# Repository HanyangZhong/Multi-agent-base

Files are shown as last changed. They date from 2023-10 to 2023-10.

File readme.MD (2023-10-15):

# 1.Hardware connection of the burgerbot drive board
d442afaf809981fc043d6bcae772b21
821f4247668aef92b34aded4d3898d7

## Connecting the drive board TB220A1

Take the driver board from the front, with the switch facing the left hand position        
Take this as a positive aspect        


The motor on the left is the right motor 'PWMB' timing in the encoder1 code corresponding to 'PWMB', with a default direction of forward rotation
The motor on the right is the left motor 'PWMA' timing in the encoder1 code corresponding to 'PWMA', with the default direction turning backwards

## Wire Connection：
The input terminal of the drive board is connected to a power supply of less than 15V, preferably 12V        
The corresponding motor is 'MG513P30_ 12V'        
        
Left white slot connected to the physical position of the car, left motor        
Right white slot connected to the physical position of the car Right motor        
        
EncoderIO：        
```
GND -- arduino mega GND
E2A  -- arduino mega 19
E2B  -- arduino mega 18
E1A  -- arduino mega 21
E1B  -- arduino mega 20
5V  None
```

c3236ec6e28d0965030df91bf430cfb
7beadca7b2e9b9cac09d8948b6bce38



DriverBoardIO：        
```
PWMB -- arduino mega 10
BIN2  -- arduino mega 9
BIN1  -- arduino mega 8
STBY  -- arduino mega 7
AIN1 -- arduino mega 5
AIN2 -- arduino mega 4
PWMA -- arduino mega 3
```

# 2.Arduino wire connection Test
## 1. Motor rotation test
Test whether the two motors can rotate normally using the 'TB6612motor' Arduino project          

## 2. Encoder testing
Use 'encoder1' as the Arduino project to test the readings of two encoders separately        

```
// motor1
//int motor_A = 21;//Interrupt port is 2
//int motor_B = 20;//Interrupt port is 3
//motor2
int motor_A = 18;//Interrupt port is 5
int motor_B = 19;//Interrupt port is 4

//Annotate the other when using pairs
...

void setup() {
  Serial.begin(57600);//
  pinMode(motor_A,INPUT);
  pinMode(motor_B,INPUT);
//
//  attachInterrupt(2,count_A,CHANGE);//Trigger interrupt function when level changes
//  //Quadruple frequency statistics require adding interrupts for phase B as well
//  attachInterrupt(3,count_B,CHANGE);

  attachInterrupt(5,count_A,CHANGE);//Trigger interrupt function when level changes
  //Quadruple frequency statistics require adding interrupts for phase B as well
  attachInterrupt(4,count_B,CHANGE);
}

```

# 3.Arduino Bridge Test
By configuring the wiring and IO port of 'TB220A1', you can directly burn and write the arduino bridge file to 'Mega2560', and then start testing        
## 1.Test encoder rotation
'e' is the number of test encoders        
'r' is the reset encoder count        
After testing the left and right wheels in the correct direction and direction, proceed to the next step of testing        
        



## 2.Test motor drive
'm' is motor speed control        
'm 100 0' is the forward movement of the left motor at a speed of 100 seconds        
Then set 'm 0 0'        



## 3.PID debugging
After testing the motor rotation and encoder function, start testing the PID        
In diff_ Under controller. h, change the test PID parameters        
Test doPID left and right wheels separately, remember to uncomment and restore after testing is completed        

```

SetPointInfo leftPID, rightPID;

/* PID Parameters */
int Kp = 17;
int Kd = 13;
int Ki = 0;
int Ko = 50;

...

void doPID(SetPointInfo * p) {
  long Perror;
  long output;
  int input;

  //Perror = p->TargetTicksPerFrame - (p->Encoder - p->PrevEnc);
  //Real time speed=Current encoder value - Last encoder end value (1/30 seconds)
  input = p->Encoder - p->PrevEnc;
  // Error=target value - current speed value
  Perror = p->TargetTicksPerFrame - input;
    //Print and use a serial plotter to test and adjust the pid
//  Serial.println(input);/

....

//Adjust the pid of the left and right wheels separately
  //doPID(&rightPID);
  doPID(&leftPID);

```

## 4.Ros-arduino-bridge yaml File Configuration
The main startup files are in 'ROS_Arduino_Bridge/Ros_Arduino_Python/launch'.        
Among them, 'my_ arduino_params' is the default file name        
Copy and rename under 'config', enter the following parameters        
```
# For a direct USB cable connection, the port name is typically
# /dev/ttyACM# where is # is a number such as 0, 1, 2, etc
# For a wireless connection like XBee, the port is typically
# /dev/ttyUSB# where # is a number such as 0, 1, 2, etc.

port: /dev/ttyACM0 #Set as appropriate, usually set to/dev/ttyACM0 or/dev/ttyUSB0
baud: 57600 #
timeout: 0.1 #

rate: 50
sensorstate_rate: 10

use_base_controller: True  #Enable Base Controller
base_controller_rate: 10   

# For a robot that uses base_footprint, change base_frame to base_footprint
base_frame: base_footprint #base_frame set up

# === Robot drivetrain parameters
wheel_diameter: 0.085 #Wheel diameter
wheel_track: 0.212    #0.244 -0.032 #Wheel spacing
encoder_resolution: 1560 #Encoder accuracy (number of pulses per cycle * frequency doubling * deceleration ratio)
#gear_reduction: 1 #reduction ratio
#motors_reversed: False #Reverse steering

# === PID parameters PID Parameters that need to be adjusted by oneself
Kp: 17
Kd: 13
Ki: 0
Ko: 50
accel_limit: 1.0

# === Sensor definitions.  Examples only - edit for your robot.
#     Sensor type can be one of the follow (case sensitive!):
#      * Ping
#      * GP2D12
#      * Analog
#      * Digital
#      * PololuMotorCurrent
#      * PhidgetsVoltage
#      * PhidgetsCurrent (20 Amp, DC)

sensors: {
  #motor_current_left:   {pin: 0, type: PololuMotorCurrent, rate: 5},
  #motor_current_right:  {pin: 1, type: PololuMotorCurrent, rate: 5},
  #ir_front_center:      {pin: 2, type: GP2D12, rate: 10},
  #sonar_front_center:   {pin: 5, type: Ping, rate: 10},
  arduino_led:          {pin: 13, type: Digital, rate: 5, direction: output}
}

```

Before running the bridge's launch file, it is necessary to 'ros_arduino_python/nodes/arduino_node.py' Setting executable permissions for files under 'node.py'        
```
sudo chmod +x arduino_node.py
```

# 4.Distributed communication configuration
## 0.Wifi Connections setting up        
1.Hardware preparation: Use a display screen or HDMI acquisition card to connect to Raspberry Pi and start it;        
2.Connect the Raspberry Pi to a wireless network;        
3.Configure static IP for Raspberry Pi, as shown in the figure        





## 1.System File Configuration
### Necessary dependency installation
The SSH implementation architecture is divided into two parts: client and server. The client is the sender of data, and the server is the receiver of data.         
In the current scenario, we need to send data from the PC to Raspberry Pi. Therefore, the PC belongs to the client, while Raspberry Pi belongs to the server. The specific implementation process is as follows:        
1. Install SSH client and server separately
2. Start SSH service on the server
3. Remote login of the client to the server
4. Implement data transmission
#### 1.Install SSH client and server        
By default, the Ubuntu system already has an SSH client installed, so you only need to install the server on Raspberry Pi (if Raspberry Pi is installing a service version of Ubuntu, the SSH service will be installed by default and has been set to boot automatically):        
```
sudo apt-get install openssh-server
```
If the client needs to install itself, call the following command:        
```
sudo apt-get install openssh-client
```
#### 2.Start SSH service on the server
Raspberry Pi Start SSH Service:        
```
sudo /etc/init.d/ssh start
```
Check if the service is running normally after startup:        
```
ps -e | grep ssh
```
If the startup is successful, it will include two programs: 'sshd' and 'ssh'.        
In the future, it is necessary to frequently use SSH to log in to Raspberry Pi. To simplify implementation, you can set the SSH service of Raspberry Pi to boot automatically. The command is as follows:        
```
sudo systemctl enable ssh
```
#### 3.Remote login of the client to the server
To log in to Raspberry Pi, you can call the following command:        
```
ssh Account@IP_address
```
Then, according to the prompt, enter the login password to successfully log in.        
If you exit the login, you can call the 'exit' command:        
```
exit
```
#### 4.Implement data transmission
Upload file:        
```
scp Local_file_path account@ip:Raspberry_path
```
Upload folder:        
```
scp -r Local_folder_path account@ip:Raspberry_path
```
Download files:                
```
scp account@ip:Raspberry_path Local_file_path    
```
Download folders:        
```
scp -r account@ip:Raspberry_path Local_folder_path
```
#### 3.Install Ros—Arduino-Bridge
'ROS_Arduino_Bridge' relies on the 'Python serial' feature pack. Please install this feature pack on the Raspberry Pi client first. The installation command is:            
```
sudo apt-get install python-serial
```
or            
```
sudo pip install --upgrade pyserial
```
or            
```
sudo easy_install -U pyserial
```

### configuration file    
Connect Raspberry Pi or Jetson Nano to the same WiFi network as the computer            
As 'PC: 192.168.0.101'          
As Raspberry Pi 'Pi: 192.168.0.110'            
Both the computer end and embedded controller end are set with static IPs to ensure they are in the same network segment        
Input        
```
sudo gedit /etc/hosts
```
Both the slave and host must be set        
Configure the other party's IP address        
```
127.0.0.1	localhost
127.0.1.1	zhy
192.168.0.110	raspberrypi

# The following lines are desirable for IPv6 capable hosts
::1     ip6-localhost ip6-loopback
fe00::0 ip6-localnet
ff00::0 ip6-mcastprefix
ff02::1 ip6-allnodes
ff02::2 ip6-allrouters
```

Then configure the ROS host and slave corresponding to the '. bashrc' file        
Enter 'sudo gedit. bashrc'        
Set the PC as a slave and take the main address of the host Raspberry        
```
export ROS_MASTER_URI=http://192.168.0.110:11311
export ROS_HOSTNAME=192.168.0.101
```
Set Raspberry Pi as the host, and take the address of the host Raspberry Pi as the main address        
```
export ROS_MASTER_URI=http://192.168.0.110:11311
export ROS_HOSTNAME=192.168.0.110
```

## 2.sshConnection control
Control commands such as:            
```
ssh -X wheeltec@192.168.0.110
```
Enter password and start controlling        

The host side run 'roscore', while the slave side does not need to run 'roscore' to send messages        
Note that all command lines require 'source. bashrc', otherwise the environment variables will not be refreshed        
Host side running test:        
```
roscore
rosrun turtlesim turtlesim_node 
```
Slave running test:        
```
rosrun turtlesim turtlesim_node 
```
After all tests are passed and messages can be received, you can start testing the arduino bridge control        

## 3.Remote control car test
### 1.Code transmission and compilation
Please first create a workspace on the Raspberry Pi end, enter the 'src' directory of the local workspace on the PC end, and call the program upload command:        
```
scp -r ros_arduino_bridge/ Raspberry_account@Raspberry_ip:~/workspace/src
```
Enter the workspace and compile on the Raspberry Pi end:        
```
catkin_make
```
### 2.test
Now start the Raspberry Pi program, and then start the PC program.        
#### Raspberry Pi
Start ros_arduino_bridge node:        
```
roslaunch ros_arduino_python arduino.launch
```
#### PC
Start keyboard control node：        
```
rosrun teleop_twist_keyboard teleop_twist_keyboard.py
```
If there are no abnormalities, you can now control the car's movement on the PC through the keyboard, and the PC can also use rviz to view the car's odometer information.

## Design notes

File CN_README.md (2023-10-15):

# 1.小车驱动板硬件连接
d442afaf809981fc043d6bcae772b21
821f4247668aef92b34aded4d3898d7

## 连接驱动板 TB220A1

正面拿驱动板，开关对着左手位置    
以此为正面    


左边的电机是 PWMB 对应encoder1代码里面的right电机    PWMB正时，默认方向向前转    
右边的电机是 PWMA 对应encoder1代码里面的left电机      PWMA正时，默认方向向后转    

## 接线：
驱动板输入端接15v以内电源，最好12v    
对应电机是MG513P30_12V    

左边白色插槽连小车物理位置左电机    
右边白色插槽连小车物理位置右电机    
    
编码器IO：
```
GND -- arduino mega GND
E2A  -- arduino mega 19
E2B  -- arduino mega 18
E1A  -- arduino mega 21
E1B  -- arduino mega 20
5V  不接
```

c3236ec6e28d0965030df91bf430cfb
7beadca7b2e9b9cac09d8948b6bce38



驱动IO：        
```
PWMB -- arduino mega 10
BIN2  -- arduino mega 9
BIN1  -- arduino mega 8
STBY  -- arduino mega 7
AIN1 -- arduino mega 5
AIN2 -- arduino mega 4
PWMA -- arduino mega 3
```

# 2.arduino测试
## 1. 电机转动测试
用 TB6612motor这个arduino工程分别测试两个电机是否能正常转动        

## 2. 编码器测试
用 encoder1这个arduino工程分别测试两个编码器的读数        

```
// 电机1
//int motor_A = 21;//中端口是2
//int motor_B = 20;//中断口是3
//电机2
int motor_A = 18;//中端口是5
int motor_B = 19;//中断口是4

//使用其中一个的时候注释另一个
...

void setup() {
  Serial.begin(57600);//设置波特率  
  pinMode(motor_A,INPUT);
  pinMode(motor_B,INPUT);
//使用其中一个的时候注释另一个
//  attachInterrupt(2,count_A,CHANGE);//当电平发生改变时触发中断函数
//  //四倍频统计需要为B相也添加中断
//  attachInterrupt(3,count_B,CHANGE);

  attachInterrupt(5,count_A,CHANGE);//当电平发生改变时触发中断函数
  //四倍频统计需要为B相也添加中断
  attachInterrupt(4,count_B,CHANGE);
}

```

# 3.arduino bridge测试
通过已经配置好TB220A1的接线和IO口,可以直接烧写arduino bridge文件到mega 2560中,然后开始进行测试        
## 1.测试编码器转动
e是测试编码器数量        
r是reset编码器计数        
测试好左轮和右轮的左右以及正方向正确后可以进行下一步测试        




## 2.测试电机驱动
m是电机速度控制        
m 100 0 是左电机前向运动 100速度 1s        
然后设置 m 0 0        



## 3.PID调试
在电机转动和编码器功能都测试完后,开始测试PID
在diff_controller.h下,更改测试PID参数        
一个个分开测试doPID左轮和右轮,记得在测试好后重新取消注释还原        
```

SetPointInfo leftPID, rightPID;

/* PID Parameters */
int Kp = 17;
int Kd = 13;
int Ki = 0;
int Ko = 50;

...

void doPID(SetPointInfo * p) {
  long Perror;
  long output;
  int input;

  //Perror = p->TargetTicksPerFrame - (p->Encoder - p->PrevEnc);
  //实时速度 = 当前编码器值 - 上次编码器结束值 （1/30秒）
  input = p->Encoder - p->PrevEnc;
  // 误差 = 目标值 - 当前速度值
  Perror = p->TargetTicksPerFrame - input;
    //打印 然后用串口绘图器测试调pid
//  Serial.println(input);/

....

//分别调试左右轮的pid
  //doPID(&rightPID);
  doPID(&leftPID);

```

## 4.ros arduino bridge yaml文件配置
在ros_arduino_bridge/ros_arduino_python/launch 里面是主要的启动文件        
其中my_arduino_params 是默认文件名称        
到config下复制改名,输入下面参数
```
# For a direct USB cable connection, the port name is typically
# /dev/ttyACM# where is # is a number such as 0, 1, 2, etc
# For a wireless connection like XBee, the port is typically
# /dev/ttyUSB# where # is a number such as 0, 1, 2, etc.

port: /dev/ttyACM0 #视情况设置，一般设置为 /dev/ttyACM0 或 /dev/ttyUSB0
baud: 57600 #波特率
timeout: 0.1 #超时时间

rate: 50
sensorstate_rate: 10

use_base_controller: True  #启用基座控制器
base_controller_rate: 10   

# For a robot that uses base_footprint, change base_frame to base_footprint
base_frame: base_footprint #base_frame 设置

# === Robot drivetrain parameters
wheel_diameter: 0.085 #车轮直径
wheel_track: 0.212    #0.244 -0.032 #轮间距
encoder_resolution: 1560 #编码器精度(一圈的脉冲数 * 倍频 * 减速比)
#gear_reduction: 1 #减速比
#motors_reversed: False #转向取反

# === PID parameters PID参数，需要自己调节
Kp: 17
Kd: 13
Ki: 0
Ko: 50
accel_limit: 1.0

# === Sensor definitions.  Examples only - edit for your robot.
#     Sensor type can be one of the follow (case sensitive!):
#      * Ping
#      * GP2D12
#      * Analog
#      * Digital
#      * PololuMotorCurrent
#      * PhidgetsVoltage
#      * PhidgetsCurrent (20 Amp, DC)

sensors: {
  #motor_current_left:   {pin: 0, type: PololuMotorCurrent, rate: 5},
  #motor_current_right:  {pin: 1, type: PololuMotorCurrent, rate: 5},
  #ir_front_center:      {pin: 2, type: GP2D12, rate: 10},
  #sonar_front_center:   {pin: 5, type: Ping, rate: 10},
  arduino_led:          {pin: 13, type: Digital, rate: 5, direction: output}
}

```

运行bridge的launch文件前，需要将ros_arduino_python/nodes/arduino_node.py下的文件设置可执行权限
```
sudo chmod +x arduino_node.py
```

# 4.分布式通信配置
## 0.wifi连接设置
1.硬件准备：使用显示屏或 HDMI采集卡连接树莓派并启动；        
2.为树莓派连接无线网络；        
3.为树莓派配置静态IP，具体操作如图        





## 1.系统文件配置
### 必要依赖安装
SSH实现架构上分为客户端和服务器端两大部分，客户端是数据的发送方，服务端是数据的接收方，当前场景下，我们需要从PC端发送数据到树莓派，那么PC端属于客户端，而树莓派属于服务端，整个实现具体流程是:        
1.分别安装SSH客户端与服务端        
2.服务端启动SSH服务        
3.客户端远程登陆服务端        
4.实现数据传输        
#### 1.安装SSH客户端与服务端
默认情况下，Ubuntu系统已经安装了SSH客户端，因此只需要在树莓派安装服务端即可(如果树莓派安装的是服务版的Ubuntu，默认会安装SSH服务并已设置成了开机自启动):        
```
sudo apt-get install openssh-server
```
如果客户端需要自行安装，那么调用如下命令:        
```
sudo apt-get install openssh-client
```
#### 2.服务端启动SSH服务
树莓派启动 ssh 服务:
```
sudo /etc/init.d/ssh start
```
启动后查看服务是否正常运行:        
```
ps -e | grep ssh
```
如果启动成功，会包含 sshd 与 ssh 两个程序。        
以后需要频繁的使用ssh登录树莓派，为了简化实现，可以将树莓派的ssh服务设置为开机自启动，命令如下:        
```
sudo systemctl enable ssh
```
#### 3.客户端远程登陆服务端
登陆树莓派可以调用如下命令:        
```
ssh 账号@ip地址
```
然后根据提示，录入登陆密码，即可成功登陆。        
如果退出登陆，可以调用exit命令:        
```
exit
```
#### 4.实现数据传输
上传文件:        
```
scp 本地文件路径 账号@ip:树莓派路径
```
上传文件夹:        
```
scp -r 本地文件夹路径 账号@ip:树莓派路径
```
下载文件:        
```
scp 账号@ip:树莓派路径 本地文件夹路径
```
下载文件夹:        
```
scp -r 账号@ip:树莓派路径 本地文件夹路径
```
#### 3.安装ros—arduino-bridge
ros_arduino_bridge是依赖于python-serial功能包的，请先在树莓派端安装该功能包，安装命令:        
```
sudo apt-get install python-serial
```
或        
```
sudo pip install --upgrade pyserial
```
或
```
sudo easy_install -U pyserial
```

### 配置文件
将树梅派或者jetson nano与电脑端连接到同一wifi网络下        
如PC:192.168.0.101        
如树梅派:192.168.0.110        
电脑端和嵌入式控制器端都设置静态IP,确保在同一网段下        
输入        
```
sudo gedit /etc/hosts
```
在从机和主机都要设置        
配置对方IP地址        
```
127.0.0.1	localhost
127.0.1.1	zhy
192.168.0.110	raspberrypi

# The following lines are desirable for IPv6 capable hosts
::1     ip6-localhost ip6-loopback
fe00::0 ip6-localnet
ff00::0 ip6-mcastprefix
ff02::1 ip6-allnodes
ff02::2 ip6-allrouters
```

然后配置.bashrc文件对应的ros主机和从机
输入`sudo gedit .bashrc`        
PC设置为从机,取主机树梅派地址为主                
```
export ROS_MASTER_URI=http://192.168.0.110:11311
export ROS_HOSTNAME=192.168.0.101
```
树梅派设置为主机,取主机树梅派地址为主                
```
export ROS_MASTER_URI=http://192.168.0.110:11311
export ROS_HOSTNAME=192.168.0.110
```

## 2.ssh连接控制
控制命令如:        
```
ssh -X wheeltec@192.168.0.110
```
输入密码,然后开始控制        

主机端运行roscore,从机端不需要运行roscore就能发送信息        
注意,所有命令行需要source .bashrc 否则不刷新环境变量        
主机端运行测试:        
```
roscore
rosrun turtlesim turtlesim_node 
```
从机端运行控制:
```
rosrun turtlesim turtlesim_node 
```
都测试通过可以接收消息后,可以开始测试arduino bridge控制

## 3.遥控小车测试
### 1.代码传输及编译
请先在树莓派端创建工作空间，在PC端进入本地工作空间的src目录，调用程序上传命令:        
```
scp -r ros_arduino_bridge/ 树莓派用户名@树莓派ip:~/工作空间/src
```
在树莓派端进入工作空间并编译:        
```
catkin_make
```
### 2.测试
现启动树莓派端程序，再启动PC端程序。        
#### 树莓派端
启动 ros_arduino_bridge 节点:        
```
roslaunch ros_arduino_python arduino.launch
```
#### PC端
启动键盘控制节点：        
```
rosrun teleop_twist_keyboard teleop_twist_keyboard.py
```
如无异常，现在就可以在PC端通过键盘控制小车运动了，并且PC端还可以使用rviz查看小车的里程计信息。

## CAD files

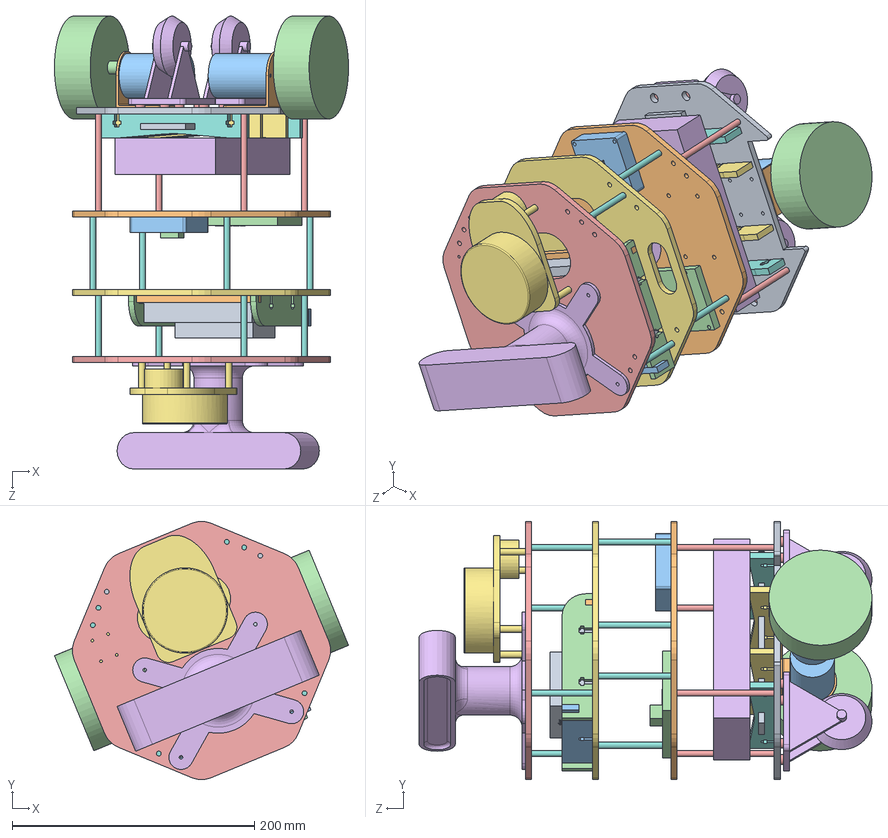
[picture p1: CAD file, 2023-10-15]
burgerbot/群小车.SLDASM
242.6 x 212.8 x 373.6 mm
底层板
motor_support x 2
motor x 2
wheel1 x 2
铜柱M5x80mm x 4
电池1
电池支撑1 x 2
电池支撑2 x 2
电池支撑3
主控板
TB6612
mega2560
support00 x 8
万向轮1 x 2
jetson主板
铜柱M5x50mm x 4
Jetson_Orin
jetson支架1
jetson支架2
jetson支架3 x 2
相机主板
深度相机
rplidar
铜柱M5x60mm x 4

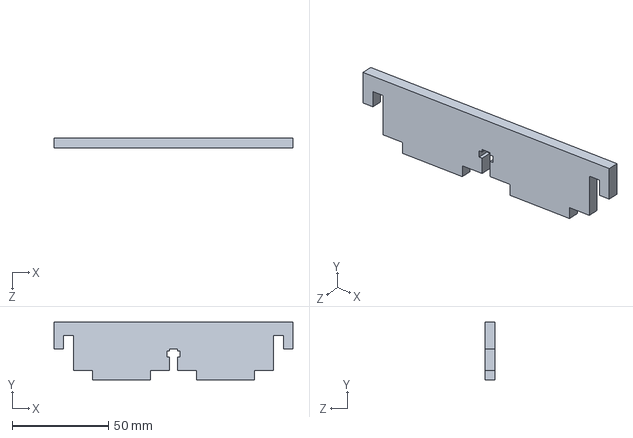
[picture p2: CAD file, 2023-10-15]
burgerbot/jetson支架2.SLDPRT
124.0 x 30.0 x 5.00 mm

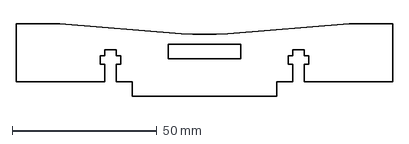
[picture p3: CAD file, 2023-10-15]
burgerbot/battery_sup1_5mm_by2.DXF
130.0 x 25.0 mm

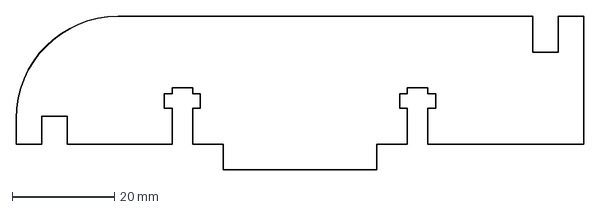
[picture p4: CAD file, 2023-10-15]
burgerbot/orinnano_sup1_5mm_by2.DXF
111.0 x 30.0 mm

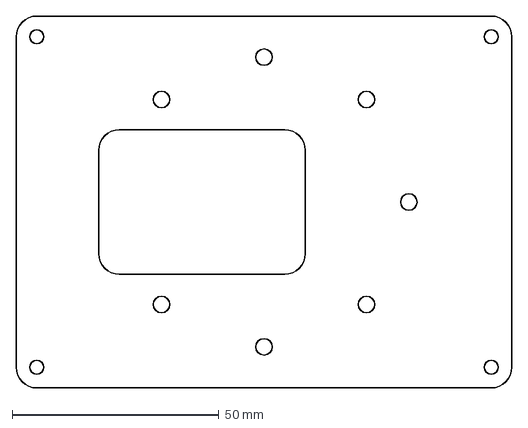
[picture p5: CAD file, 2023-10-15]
burgerbot/top_sup1_5mm_by1.DXF
120.0 x 90.0 mm

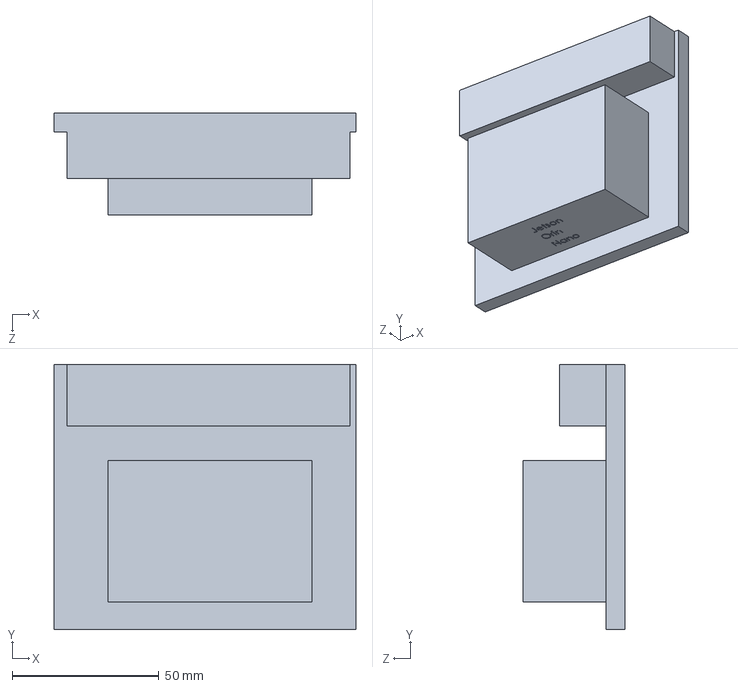
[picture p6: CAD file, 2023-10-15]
burgerbot/Jetson_Orin.SLDPRT
103.0 x 90.5 x 34.8 mm

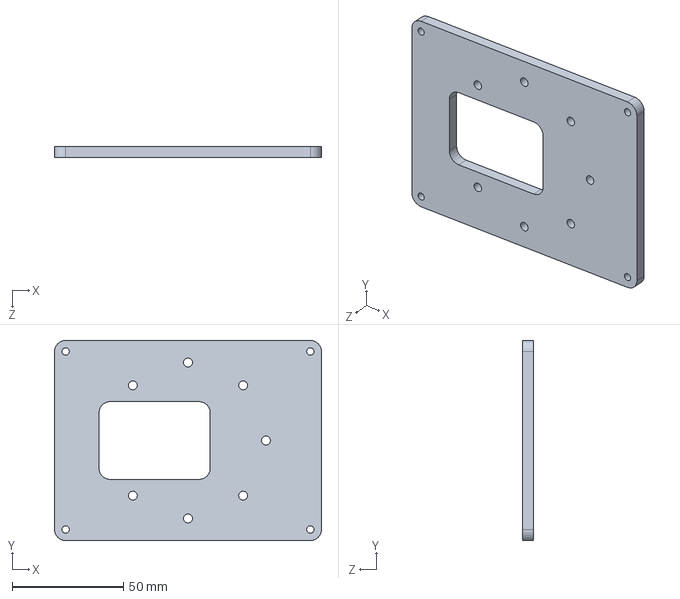
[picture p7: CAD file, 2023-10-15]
burgerbot/机械臂架2.SLDPRT
120.0 x 90.0 x 5.00 mm

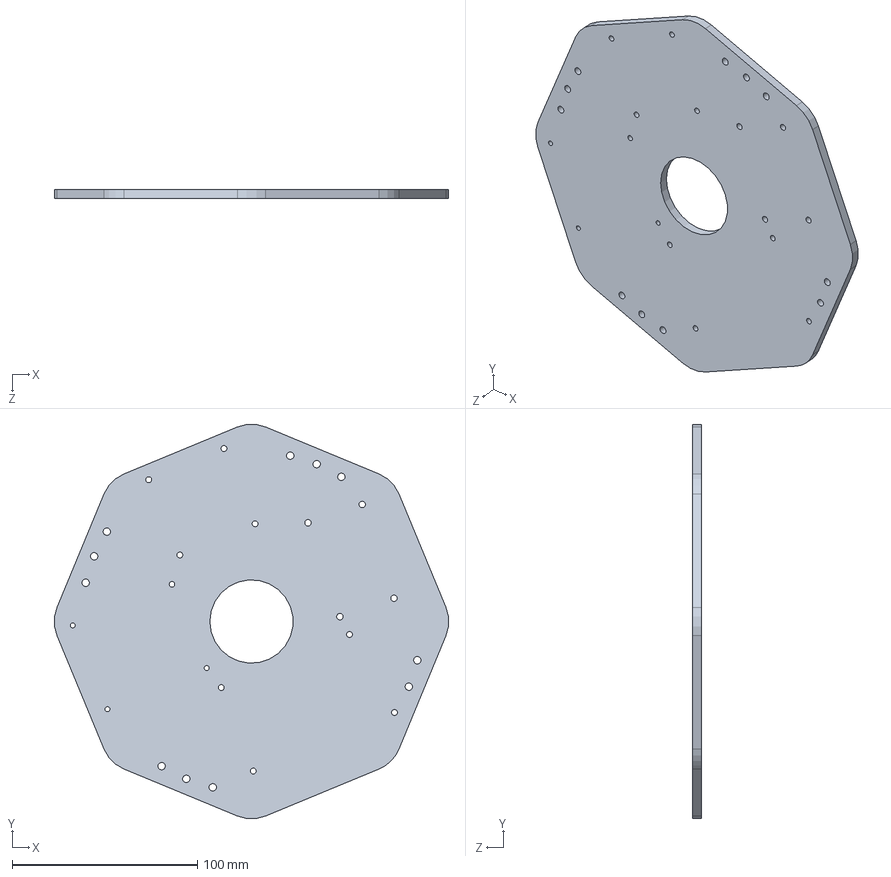
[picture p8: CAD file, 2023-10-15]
burgerbot/主控板.SLDPRT
212.8 x 212.8 x 5.00 mm

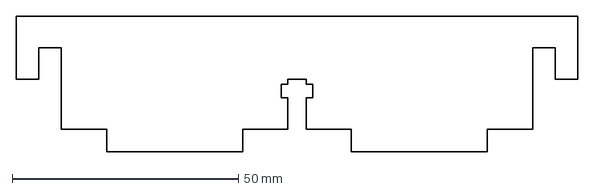
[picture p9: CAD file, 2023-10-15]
burgerbot/orinnano_sup2_5mm_by1.DXF
124.0 x 30.0 mm

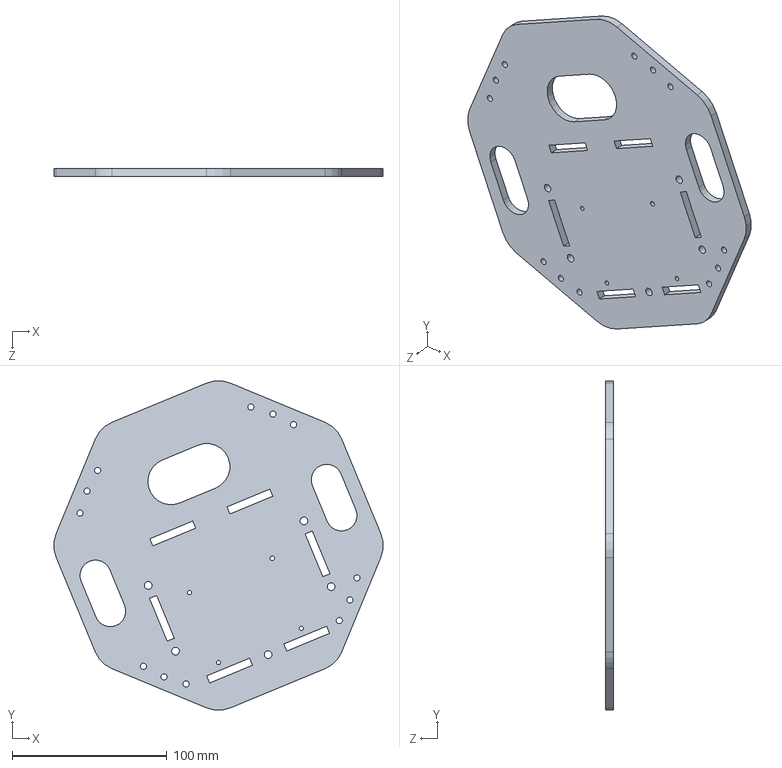
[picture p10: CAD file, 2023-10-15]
burgerbot/jetson主板.SLDPRT
212.8 x 212.8 x 5.00 mm

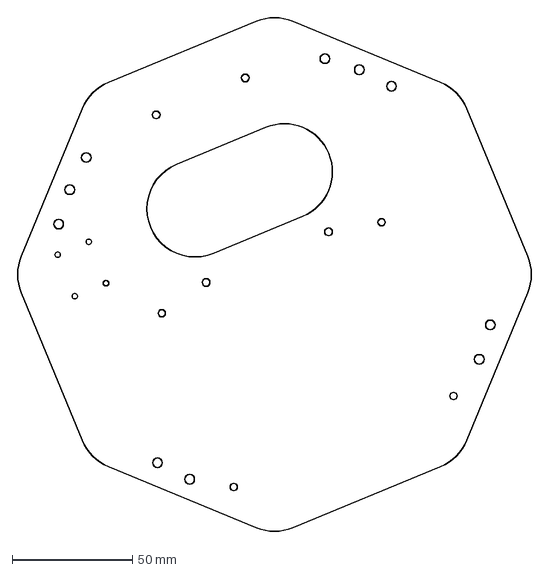
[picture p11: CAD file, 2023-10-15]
burgerbot/burgerbot_layer4_5mm_by1.DXF
214.2 x 214.2 mm

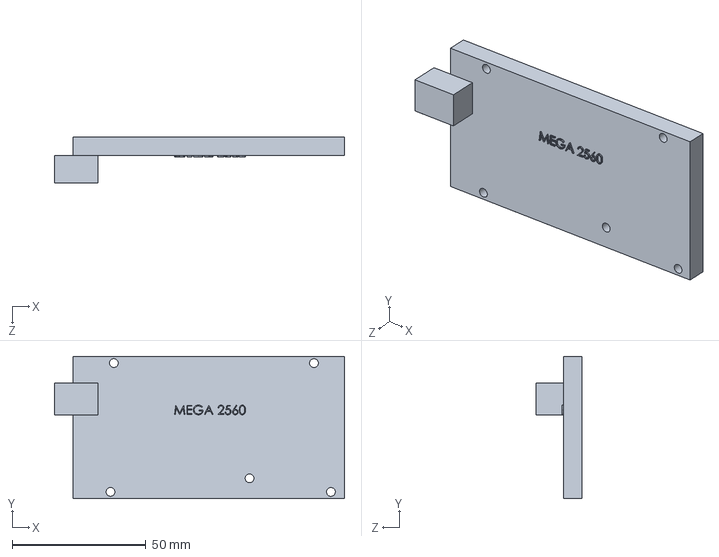
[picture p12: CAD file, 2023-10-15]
burgerbot/mega2560.SLDPRT
108.6 x 53.3 x 17.3 mm

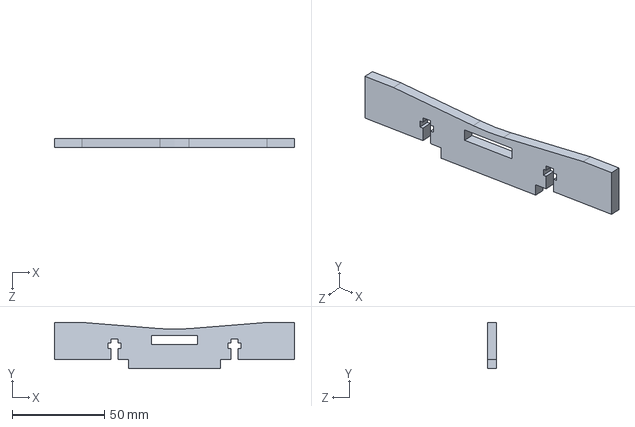
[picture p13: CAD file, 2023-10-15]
burgerbot/电池支撑1.SLDPRT
130.0 x 25.0 x 5.00 mm

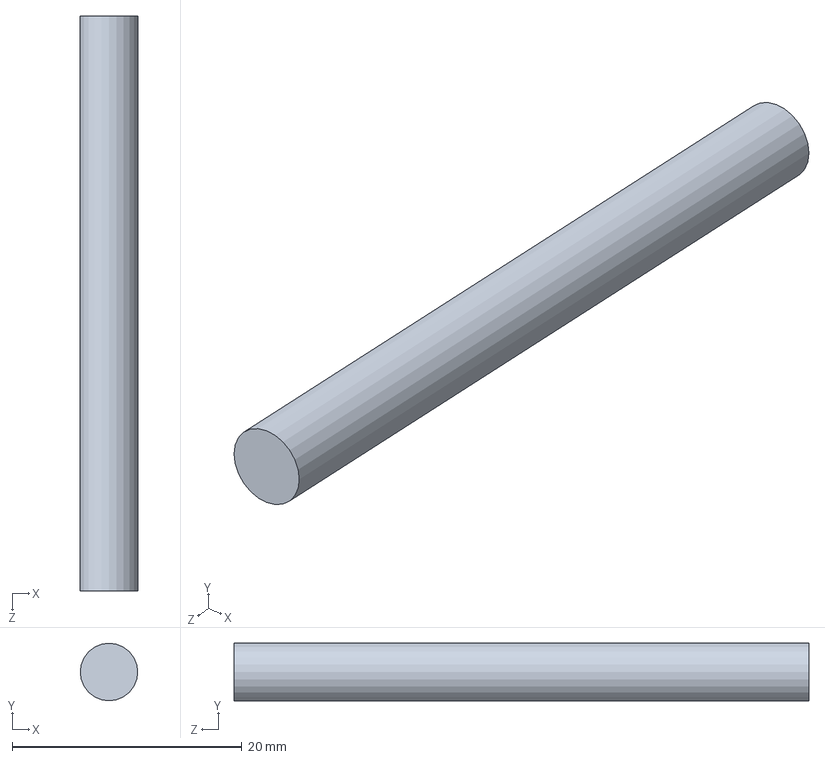
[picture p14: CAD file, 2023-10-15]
burgerbot/铜柱M5x50mm.SLDPRT
5.00 x 5.00 x 50.0 mm

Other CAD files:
burgerbot/orinnano_sup3_5mm_by1.DXF
burgerbot/wheel2.SLDPRT
burgerbot/电池支撑2.SLDPRT
burgerbot/相机主板.SLDPRT
burgerbot/TB6612.SLDPRT
burgerbot/battery_sup2_5mm_by2.DXF
burgerbot/battery_sup3_5mm_by1.DXF
burgerbot/burgerbot_layer1_5mm_by1.DXF
burgerbot/burgerbot_layer2_5mm_by1.DXF
burgerbot/burgerbot_layer3_5mm_by1.DXF
burgerbot/jetson支架1.SLDPRT
burgerbot/jetson支架3.SLDPRT
burgerbot/motor.SLDPRT
burgerbot/motor_support.SLDPRT
burgerbot/rplidar.SLDPRT
burgerbot/support0.SLDPRT
burgerbot/support00.SLDPRT
burgerbot/top_layer1_5mm_by3.DXF
burgerbot/wheel1.SLDPRT
burgerbot/万向轮1.SLDPRT
burgerbot/底层板.SLDPRT
burgerbot/树莓派.SLDPRT
burgerbot/深度相机.SLDPRT
burgerbot/电池1.SLDPRT
burgerbot/电池支撑3.SLDPRT
burgerbot/相机板.SLDPRT
burgerbot/铜柱M5x60mm.SLDPRT
burgerbot/铜柱M5x80mm.SLDPRT
burgerbot/防撞.SLDPRT
burgerbot/顶层板替换1.SLDPRT

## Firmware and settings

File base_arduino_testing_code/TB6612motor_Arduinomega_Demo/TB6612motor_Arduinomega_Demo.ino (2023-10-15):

///////////////////TB6612引脚接线///////////////////////////
//直流电机----------TB6612丝印标识----------ArduinoUNO主板引脚
//                     PWMA-----------------3
//                     AIN2-----------------4
//                     AIN1-----------------5
//                     STBY-----------------7
//                     BIN1-----------------8
//                     BIN2-----------------9
//                     PWMB-----------------10
//                     GND------------------GND
//                     ADC------------------A0 (只有带TB6612带稳压模块版才有ADC测量电池电压功能)    
//                     VM-------------------12V电池
//                     VCC------------------5V  （使用带有稳压模块版时，接线变动如下：  5V---------5V  板子可向arduino供电）
//                     GND------------------GND  
//电机A正极-------------AO1
//电机A负极-------------A02
//电机B负极-------------BO2
//电机B正极-------------BO1
//                     GND-----------------GND
//直流电机----------TB6612丝印标识----------ArduinoUNO主板引脚

//定义引脚名称
#define PWMA 3  //3为模拟引脚，用于PWM控制
#define AIN1 5
#define AIN2 4
#define PWMB 10  //10为模拟引脚，用于PWM控制
#define BIN1 8
#define BIN2 9
#define STBY 7  //2、4、8、12、7为数字引脚，用于开关量控制
#define Voltage A0 //使用模拟引脚

//赵使用
//int DIRA = 4;
//int PWMA = 5;
//int DIRB = 7;
//int PWMB = 6;

int PwmA, PwmB;
double V;

void setup() {
  //TB6612电机驱动模块控制信号初始化
  pinMode(AIN1, OUTPUT);//控制电机A的方向，(AIN1, AIN2)=(1, 0)为正转，(AIN1, AIN2)=(0, 1)为反转
  pinMode(AIN2, OUTPUT);
  pinMode(BIN1, OUTPUT);//控制电机B的方向，(BIN1, BIN2)=(0, 1)为正转，(BIN1, BIN2)=(1, 0)为反转
  pinMode(BIN2, OUTPUT);
  pinMode(PWMA, OUTPUT);//A电机PWM
  pinMode(PWMB, OUTPUT);//B电机PWM
  pinMode(STBY, OUTPUT);//TB6612FNG使能, 置0则所有电机停止, 置1才允许控制电机
  
  //初始化TB6612电机驱动模块
  digitalWrite(AIN1, 1);
  digitalWrite(AIN2, 0);
  digitalWrite(BIN1, 1);
  digitalWrite(BIN2, 0);
  digitalWrite(STBY, 1);
  analogWrite(PWMA, 0);
  analogWrite(PWMB, 0);

 //初始化串口，用于输出电池电压
  Serial.begin(9600);
  pinMode(Voltage,INPUT); //初始化作为输入端
}

/**************************************************************************
函数功能：设置指定电机转速
入口参数：指定电机motor，motor=1（2）代表电机A（B）； 指定转速pwm，大小范围为0~255，代表停转和满速
返回  值：无
**************************************************************************/
void SetPWM(int motor, int pwm)
{
  if(motor==1&&pwm>=0)//motor=1代表控制电机A，pwm>=0则(AIN1, AIN2)=(1, 0)为正转
  {
    digitalWrite(AIN1, 1);
    digitalWrite(AIN2, 0);
    analogWrite(PWMA, pwm);
  }
  else if(motor==1&&pwm<0)//motor=1代表控制电机A，pwm<0则(AIN1, AIN2)=(0, 1)为反转
  {
    digitalWrite(AIN1, 0);
    digitalWrite(AIN2, 1);
    analogWrite(PWMA, -pwm);
  }
  else if(motor==2&&pwm>=0)//motor=2代表控制电机B，pwm>=0则(BIN1, BIN2)=(0, 1)为正转
  {
    digitalWrite(BIN1, 0);
    digitalWrite(BIN2, 1);
    analogWrite(PWMB, pwm);
  }
  else if(motor==2&&pwm<0)//motor=2代表控制电机B，pwm<0则(BIN1, BIN2)=(1, 0)为反转
  {
    digitalWrite(BIN1, 1);
    digitalWrite(BIN2, 0);
    analogWrite(PWMB, -pwm);
  }
}

void loop() 
{
  SetPWM(2, 255);//电机AB同时满速正转
  SetPWM(1, 0);
//  V=analogRead(Voltage); //读取模拟引脚A0模拟量
//  Serial.print(V*0.05371);  //对模拟量转换并通过串口输出
//  Serial.println("V");

  delay(1000);//正转3s
  Serial.println("running");
  SetPWM(1, 0);//电机AB停止
  SetPWM(2, 0);
  delay(1000);//停止1s
//  
//  SetPWM(1, 128);//电机AB同时半速正转
//  SetPWM(2, 128);
//  delay(3000);//半速正转3s
//  
//  SetPWM(1, 0);//电机AB停止
//  SetPWM(2, 0);
//  delay(1000);//停止1s
//  
//  SetPWM(1, -255);//电机AB同时满速反转
//  SetPWM(2, -255);
//  delay(3000);//反转3s
//  
//  SetPWM(1, 0);//电机AB停止
//  SetPWM(2, 0);
//  delay(1000);//停止1s
//  
//  SetPWM(1, 255);//电机A满速正转
//  SetPWM(2, -255);//电机B满速反转
//  delay(3000);//持续3s
//  
//  SetPWM(1, 0);//电机AB停止
//  SetPWM(2, 0);
//  delay(1000);//停止1s
}

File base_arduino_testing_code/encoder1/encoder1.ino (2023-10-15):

/*
 * 测速实现:
 *  阶段1:脉冲数统计
 *  阶段2:速度计算
 * 
 * 阶段1:
 *  1.定义所使用的中断引脚,以及计数器(使用 volatile 修饰)
 *  2.setup 中设置波特率，将引脚设置为输入模式
 *  3.使用 attachInterupt() 函数为引脚添加中断出发时机以及中断函数
 *  4.中断函数编写计算算法，并打印
 *    A.单频统计只需要统计单相上升沿或下降沿
 *    B.2倍频统计需要统计单相的上升沿和下降沿
 *    C.4倍频统计需要统计两相的上升沿和下降沿
 *  5.上传并查看结果
 *  
 * 
 */
// 电机1
int motor_A = 21;//中端口是2
int motor_B = 20;//中断口是3
//电机2
//int motor_A = 18;//中端口是5
//int motor_B = 19;//中断口是4
volatile int count = 0;//如果是正转，那么每计数一次自增1，如果是反转，那么每计数一次自减1 


void count_A(){
  //单频计数实现
  //手动旋转电机一圈，输出结果为 一圈脉冲数 * 减速比
  /*if(digitalRead(motor_A) == HIGH){

    if(digitalRead(motor_B) == LOW){//A 高 B 低
      count++;  
    } else {//A 高 B 高
      count--;  
    }


  }*/

  //2倍频计数实现
  //手动旋转电机一圈，输出结果为 一圈脉冲数 * 减速比 * 2
  if(digitalRead(motor_A) == HIGH){

    if(digitalRead(motor_B) == HIGH){//A 高 B 高
      count++;  
    } else {//A 高 B 低
      count--;  
    }


  } else {

    if(digitalRead(motor_B) == LOW){//A 低 B 低
      count++;  
    } else {//A 低 B 高
      count--;  
    }  

  }

}

//与A实现类似
//4倍频计数实现
//手动旋转电机一圈，输出结果为 一圈脉冲数 * 减速比 * 4
void count_B(){
  if(digitalRead(motor_B) == HIGH){

    if(digitalRead(motor_A) == LOW){//B 高 A 低
      count++;
    } else {//B 高 A 高
      count--;
    }


  } else {

    if(digitalRead(motor_A) == HIGH){//B 低 A 高
      count++;
    } else {//B 低 A 低
      count--;
    }

  }

}

void setup() {
  Serial.begin(57600);//设置波特率  
  pinMode(motor_A,INPUT);
  pinMode(motor_B,INPUT);
  attachInterrupt(2,count_A,CHANGE);//当电平发生改变时触发中断函数
//  //四倍频统计需要为B相也添加中断
  attachInterrupt(3,count_B,CHANGE);

//  attachInterrupt(5,count_A,CHANGE);//当电平发生改变时触发中断函数
  //四倍频统计需要为B相也添加中断
//  attachInterrupt(4,count_B,CHANGE);
}


void loop() {
  //测试计数器输出
  delay(2000);
  Serial.println(count);

}
